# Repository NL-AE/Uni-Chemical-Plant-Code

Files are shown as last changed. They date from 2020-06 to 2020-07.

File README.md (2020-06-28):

# Uni-Chemical-Plant-Code
Code for two-way I2C communication between two Arduino nanos.
One drives the 2.4” TFT LCD display and the other controls all of the pumps.

The control Arduino also sends out serial data at 115200 baud rate in the format of:
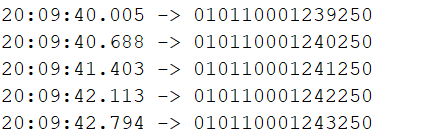
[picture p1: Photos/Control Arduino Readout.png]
Readout

Breakdown

Fresh interface in a simplified P&ID (Piping and instrumentation diagram)
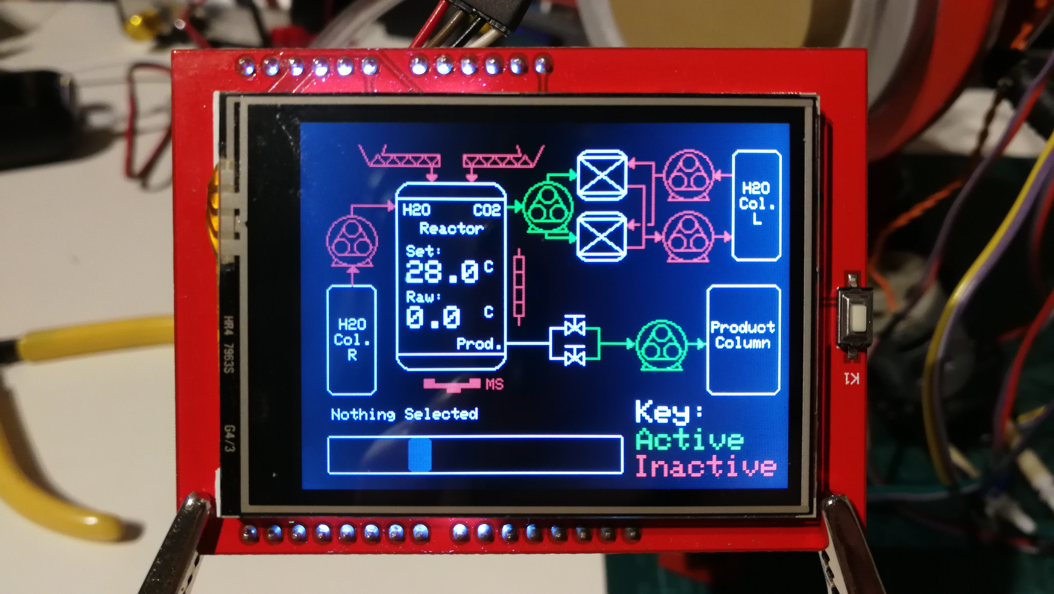
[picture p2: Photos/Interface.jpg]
Interface


Schematic
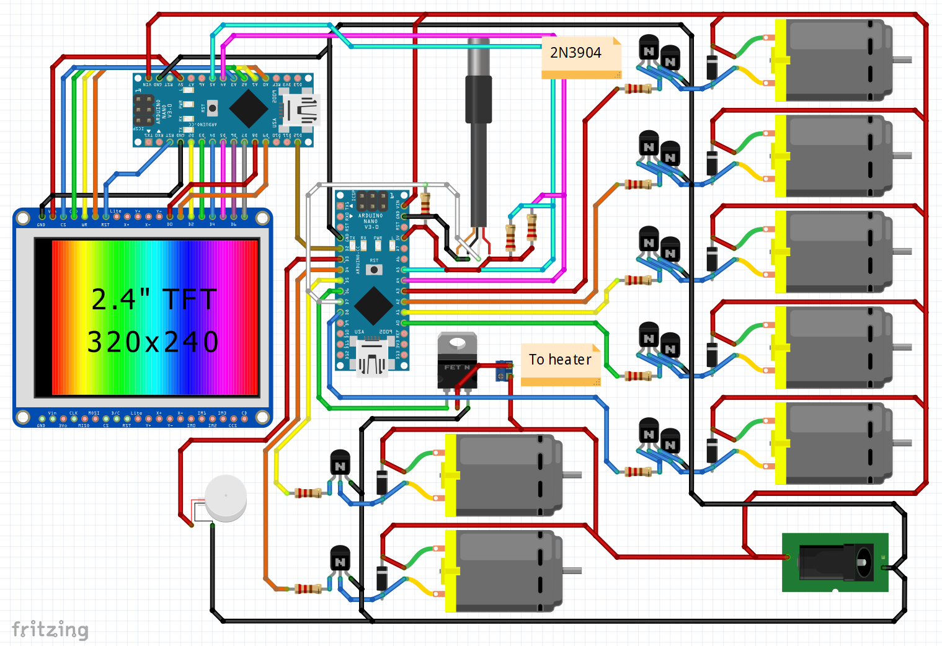
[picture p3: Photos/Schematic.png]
Schematic


Code Flowchart
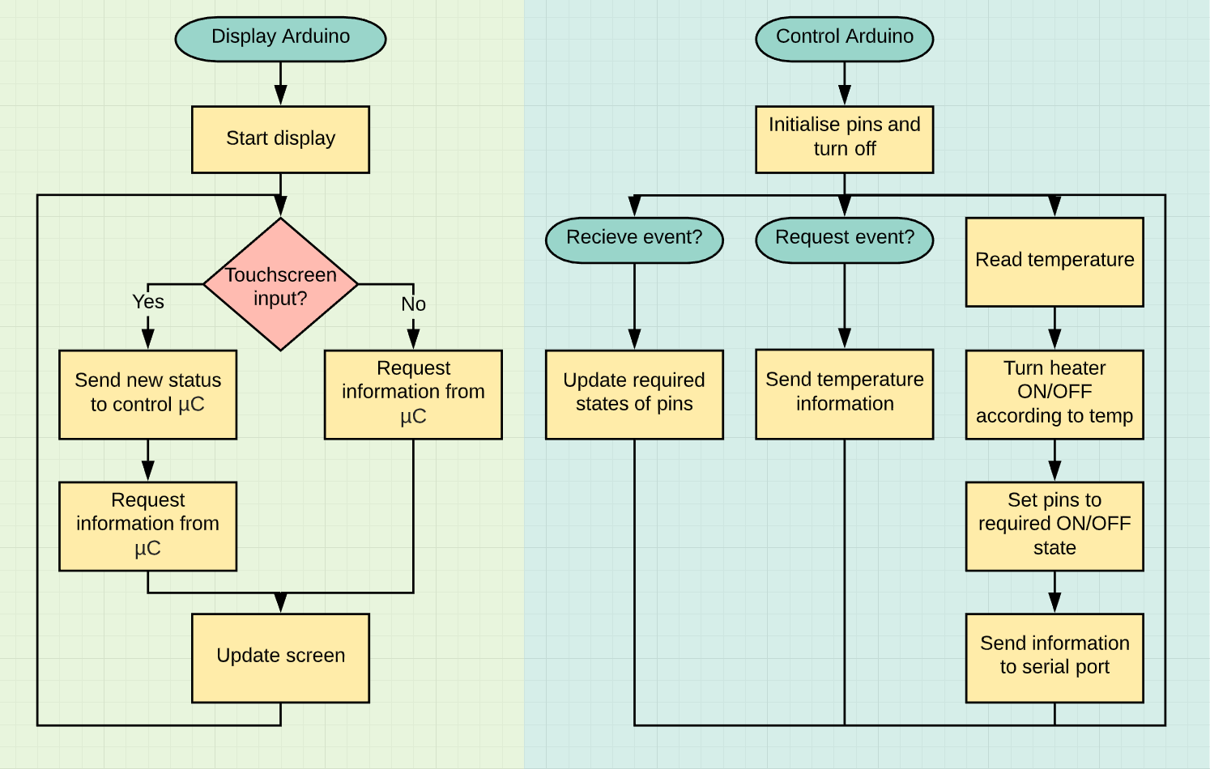
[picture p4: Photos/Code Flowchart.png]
Code_Flowchart


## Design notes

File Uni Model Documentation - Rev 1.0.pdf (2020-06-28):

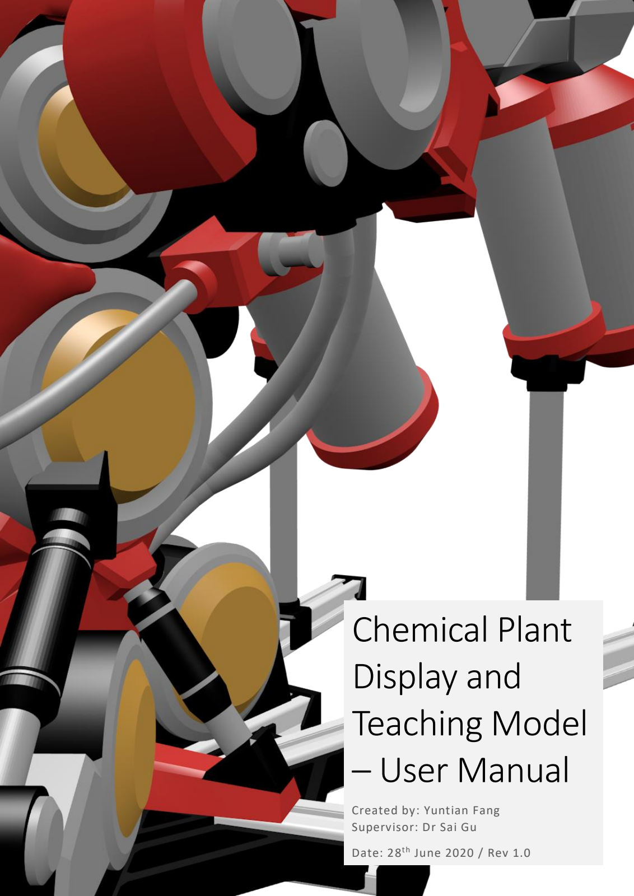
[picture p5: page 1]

# Chemical Plant Display and Teaching Model – User Manual

Created by: Yuntian Fang
Supervisor: Dr Sai Gu

Date: 28

th June 2020 / Rev 1.0

## Introduction

This fully 3D printed model of a basic chemical plant is intended to be used as a display and simple teaching model with all the functionality of a real chemical plant in an aesthetically appealing package.

Controlled by the touchscreen on the front and powered just by a generic 12V 3A mains plug, the model is entirely self-contained and is very simple to set up. It simply needs to be plugged in to power and the microprocessors will automatically begin.

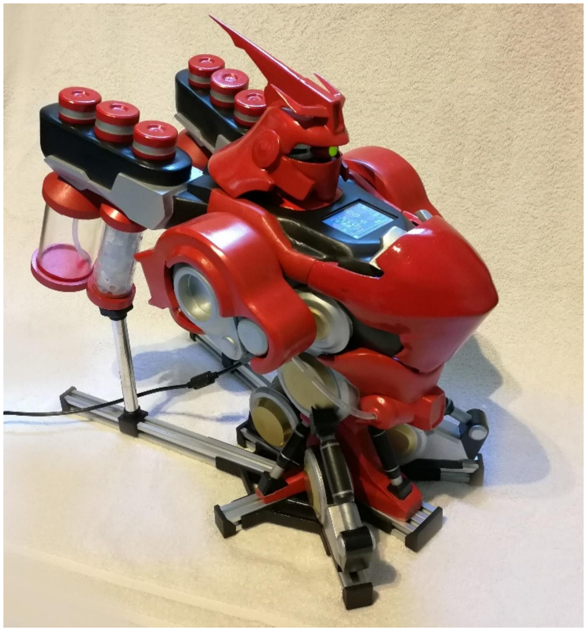
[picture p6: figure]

Figure 1: Fully assembled model powered on. Dimensions are (WxLxH): 25cm x 50cm x 43cm.

## Functionality

The model contains following parts:

- 2 x screw feeders into the main reactor for solid-based reactants.
- 1 x liquid reactant holder with delivery to reactor vessel (removable).
- 1 x CO2 extraction vessel using a water scrubbing system.
- 1 x CO2 scrubbing water storage vessel (removable).
- 1 x Reactant storage vessel (removable).
- 1 x Reactor vessel.
- Temperature controlled to the nearest 0.1oC.
- Magnetic stirrer.
- USB mini output to computer.
- 2.4” touchscreen with P&ID schematic interface.

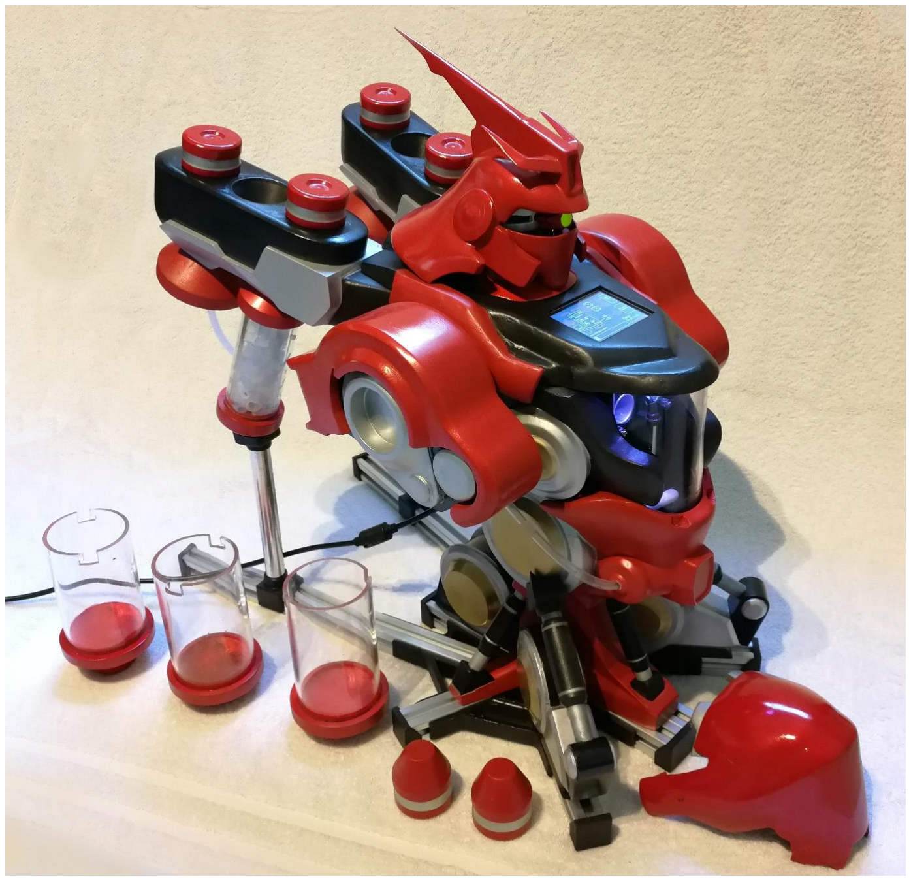
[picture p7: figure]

Figure 2: Model with parts removed exposing the reactor vessel and screw feeder input holes.

## Specific Areas of Interest

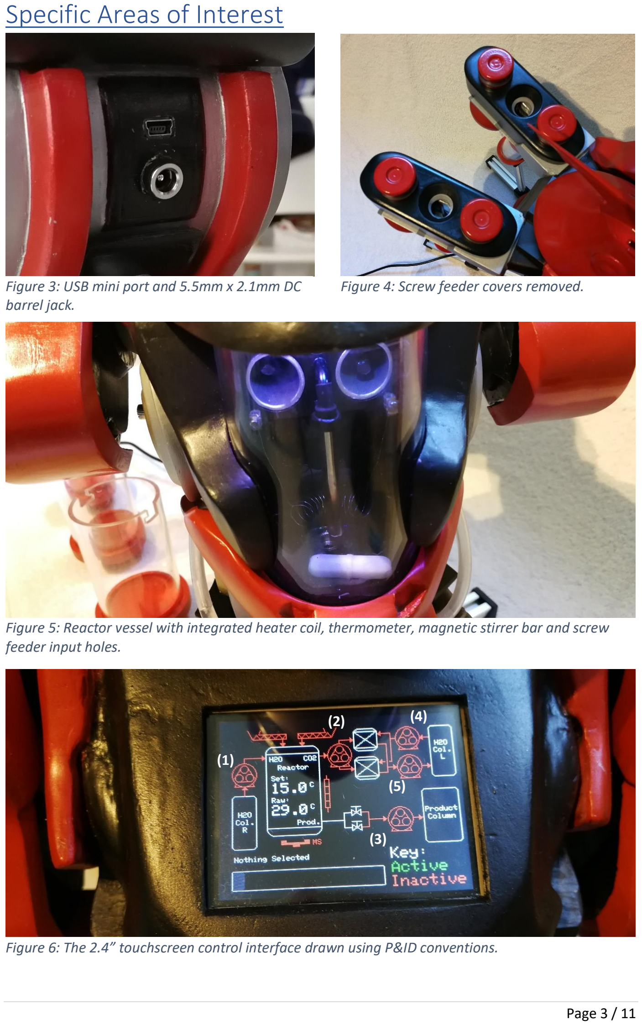
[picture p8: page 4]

Figure 3: USB mini port and 5.5mm x 2.1mm DC barrel jack.

Figure 4: Screw feeder covers removed.

Figure 5: Reactor vessel with integrated heater coil, thermometer, magnetic stirrer bar and screw feeder input holes.

Figure 6: The 2.4” touchscreen control interface drawn using P&ID conventions.

(1)

(2)

(3)

(4)

(5)

## Mode of Operation

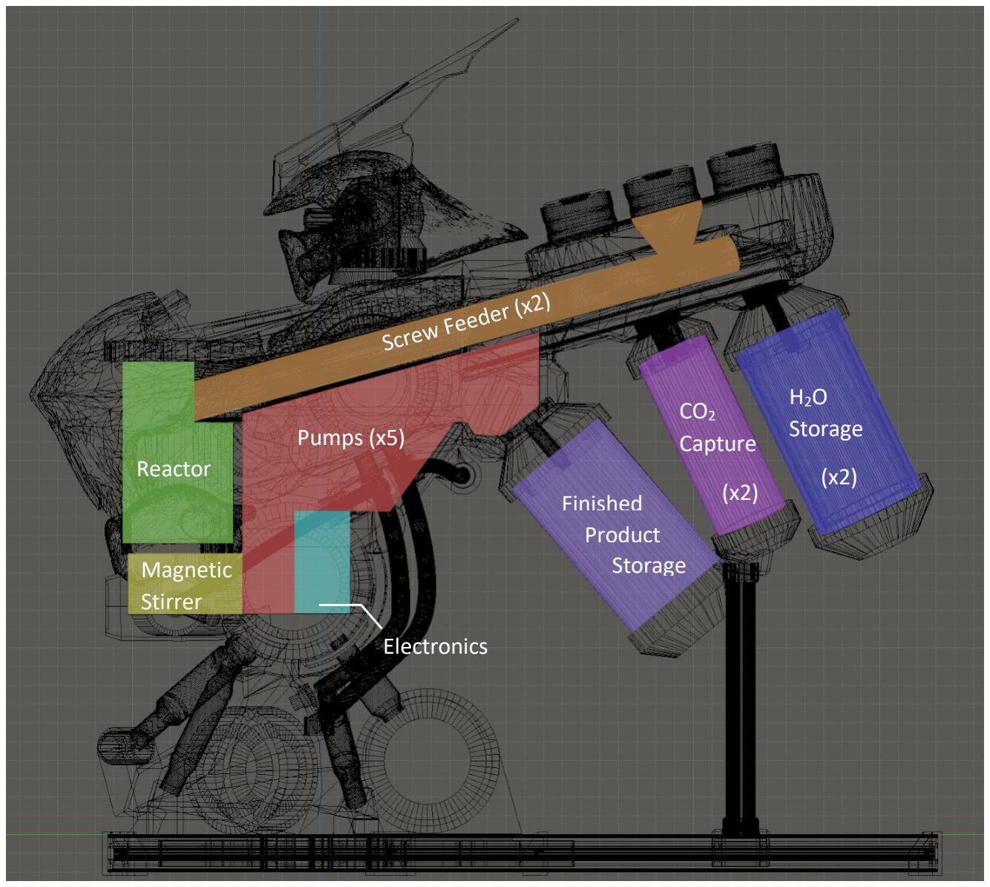
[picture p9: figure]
Reactor; Pumps (x5); Electronics; H2O Storage; CO2 Capture; Magnetic Stirrer; Finished Product Storage

Inside the model, there are five self-priming peristaltic pumps to move liquids around and two DC motors that control the screw feeders.

As per the P&ID diagram before,

- Pump 1 : Moves water from the H2O column on the right directly into the reactor.
- Pump 2 : Removes CO2 and transfers it to the CO2 capture column. Only the column on the left will function due to technical difficulties.
- Pump 3 : Transfers the liquid product from the reactor into the finished product storage column.
- Pump 4 : Supplies water to the CO2 scrubber from the H2O column on the left.
- Pump 5 : Returns water from CO2 scrubber back to left H2O column.

Figure 7: Highlighted and labelled areas of the model.

## Notes for Usage and Safety

1) Power and USB connection:
a. Power the model with a 12V supply (±1V) with at least 3A capability through the DC barrel jack.
b. Do NOT connect to computer without plugging into power BEFOREHAND.
c. ALWAYS remove USB connection BEFORE removing 12V power.
d. Failure to comply with notes 1b and 1c may cause the microcontroller to crash or other erratic behaviour not limited to permeant damage to the microcontroller and the PC it is connected to.
2) Operating pumps:
a. Do NOT allow the following pumps to operate without supervision.
i. Pump 1 – Moves water into the reactor.
ii. Pump 3 – Moves liquid from reactor to product storage. These pumps control liquid flow in and out of the reactor which can overflow.
This is due to the lack of feedback systems from the additional complexity of monitoring systems and hysteresis from the relatively large volume contained inside the connecting pipes.
b. Pumps 4 and 5 should be operational at the same time during continuous operation and should only differ during start-up (to add some water into the capture column) and during shut down (to remove all water from the column.)
c. Pump 2 can be operated in any situation.
3) Screw feeders:
a. Do NOT pour liquids into the mechanism. If cleaning is needed use compressed air or other non-liquid method.
b. Replace cover after use to prevent the screw from being jammed by any external objects that may enter.
4) Reactor and storage columns:
a. Do NOT allow reactor to overflow.
b. Empty them out after purging all water from system.
c. Do NOT set the heater temperature to higher than raw without there being water in the reactor.
5) Top cover
a. Can be removed and replaced to expose internals. Held on by friction. May require a gentle push to lock into place. Do not force.

## Design and Electronics

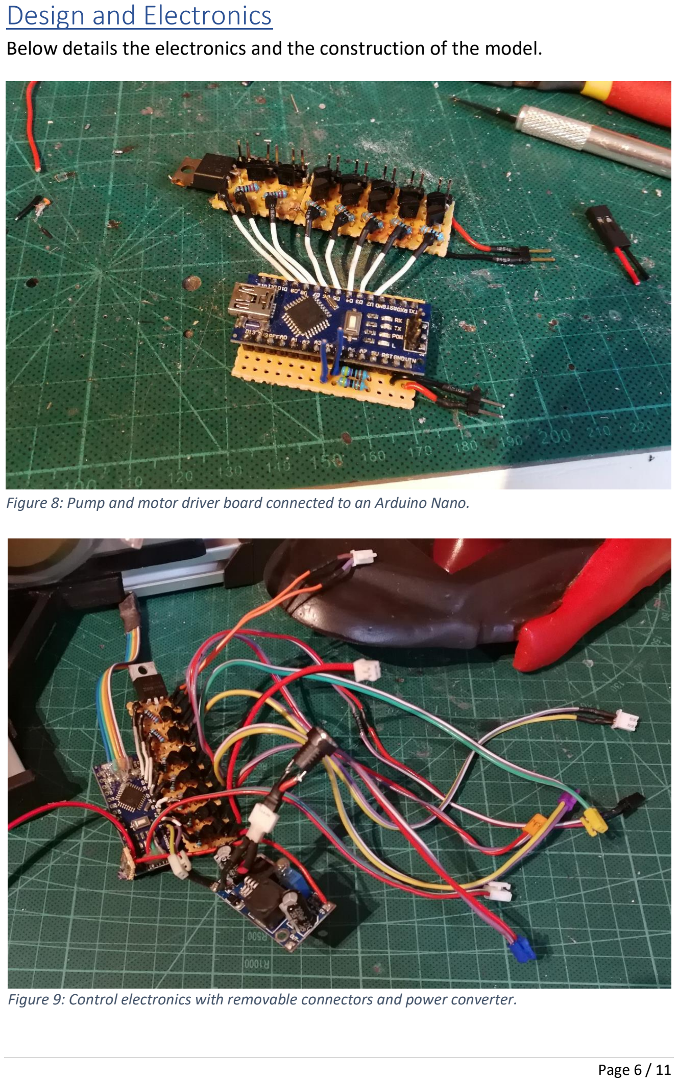
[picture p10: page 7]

Below details the electronics and the construction of the model.

Figure 8: Pump and motor driver board connected to an Arduino Nano.

Figure 9: Control electronics with removable connectors and power converter.

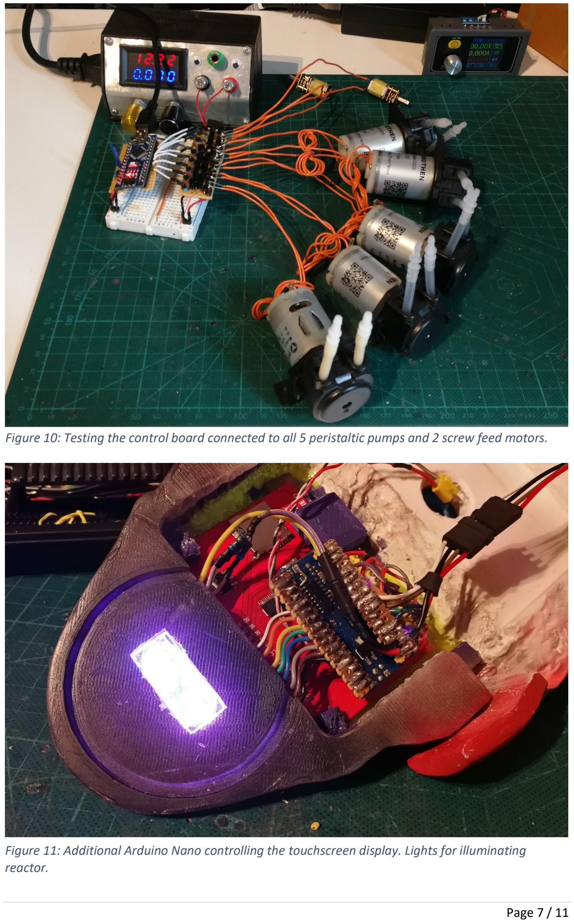
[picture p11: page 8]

Figure 10: Testing the control board connected to all 5 peristaltic pumps and 2 screw feed motors.

Figure 11: Additional Arduino Nano controlling the touchscreen display. Lights for illuminating reactor.

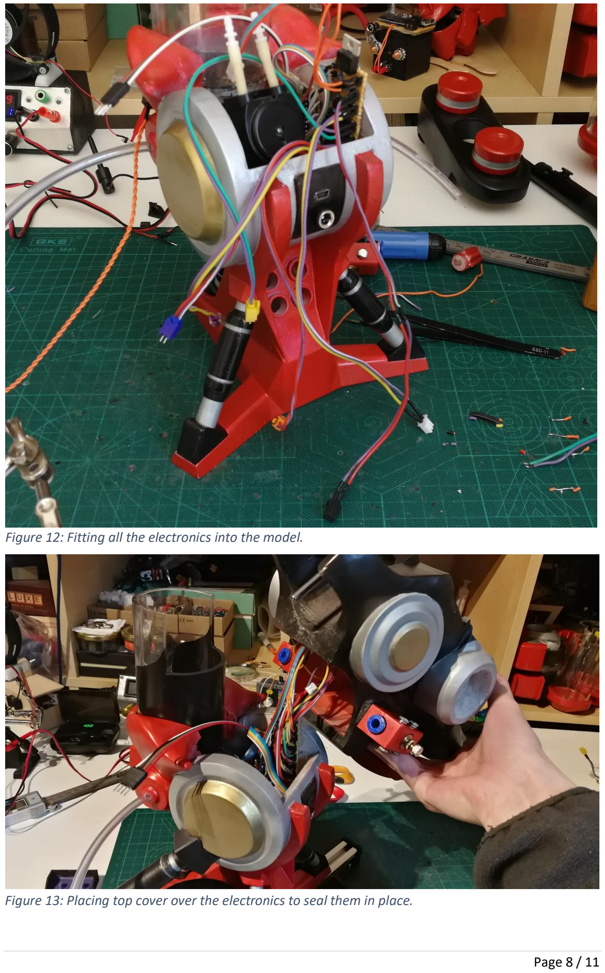
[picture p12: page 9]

Figure 12: Fitting all the electronics into the model.

Figure 13: Placing top cover over the electronics to seal them in place.

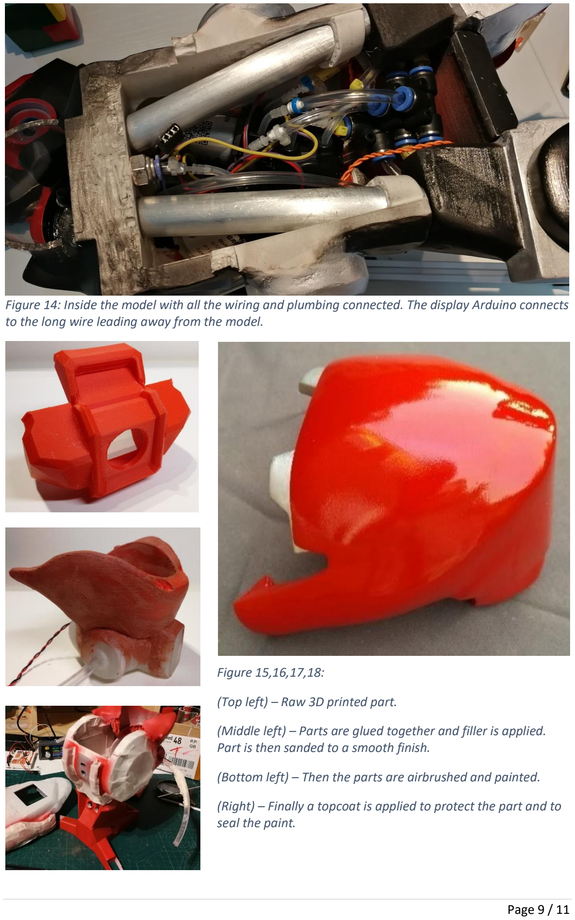
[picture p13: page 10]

Figure 14: Inside the model with all the wiring and plumbing connected. The display Arduino connects to the long wire leading away from the model.

Figure 15,16,17,18:

(Top left) – Raw 3D printed part.

(Middle left) – Parts are glued together and filler is applied. Part is then sanded to a smooth finish.

(Bottom left) – Then the parts are airbrushed and painted.

(Right) – Finally a topcoat is applied to protect the part and to seal the paint.

## References/Technical Information

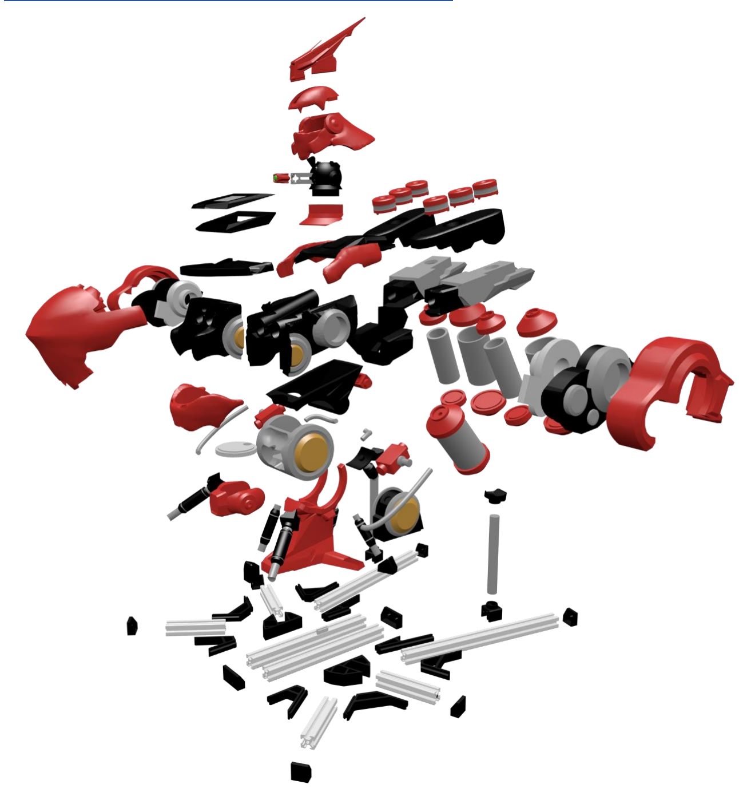
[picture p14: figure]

Following describes the more technical details of the model including the code and how the model operates.

The code can be freely downloaded at my GitHub:

https://github.com/NL-AE/Uni-Chemical-Plant-Code

The following information is also available on the README file in the GitHub and is copied here for convenience.

Figure 19: Exploded view of all the parts in the model.

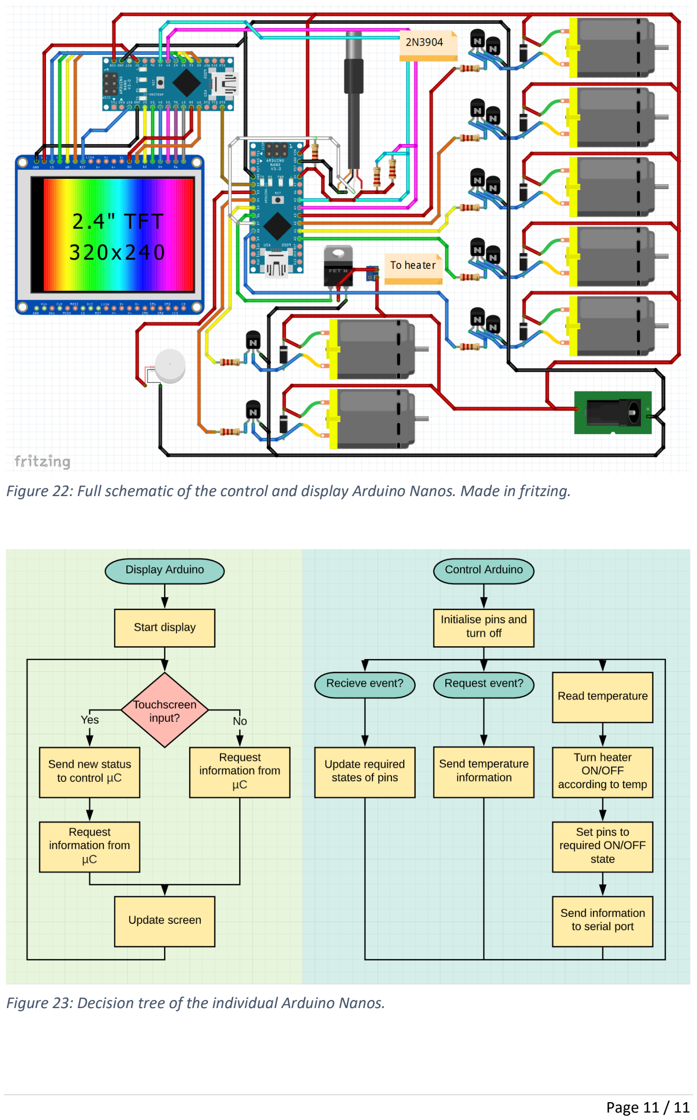
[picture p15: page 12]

Figure 22: Full schematic of the control and display Arduino Nanos. Made in fritzing.

Figure 23: Decision tree of the individual Arduino Nanos.

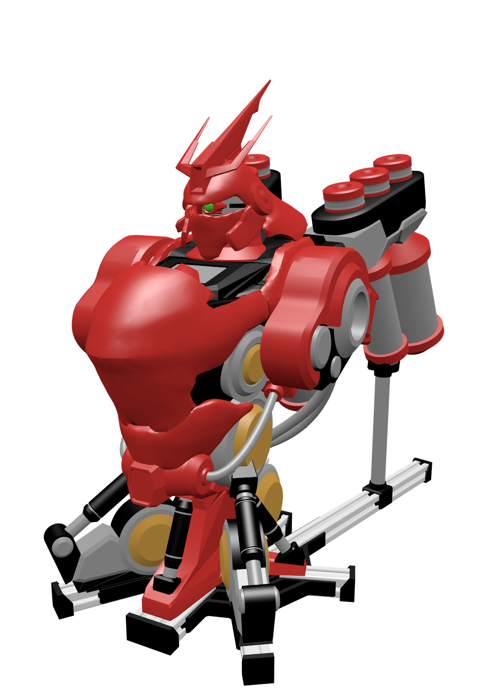
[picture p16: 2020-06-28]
Photos/3D Render.png

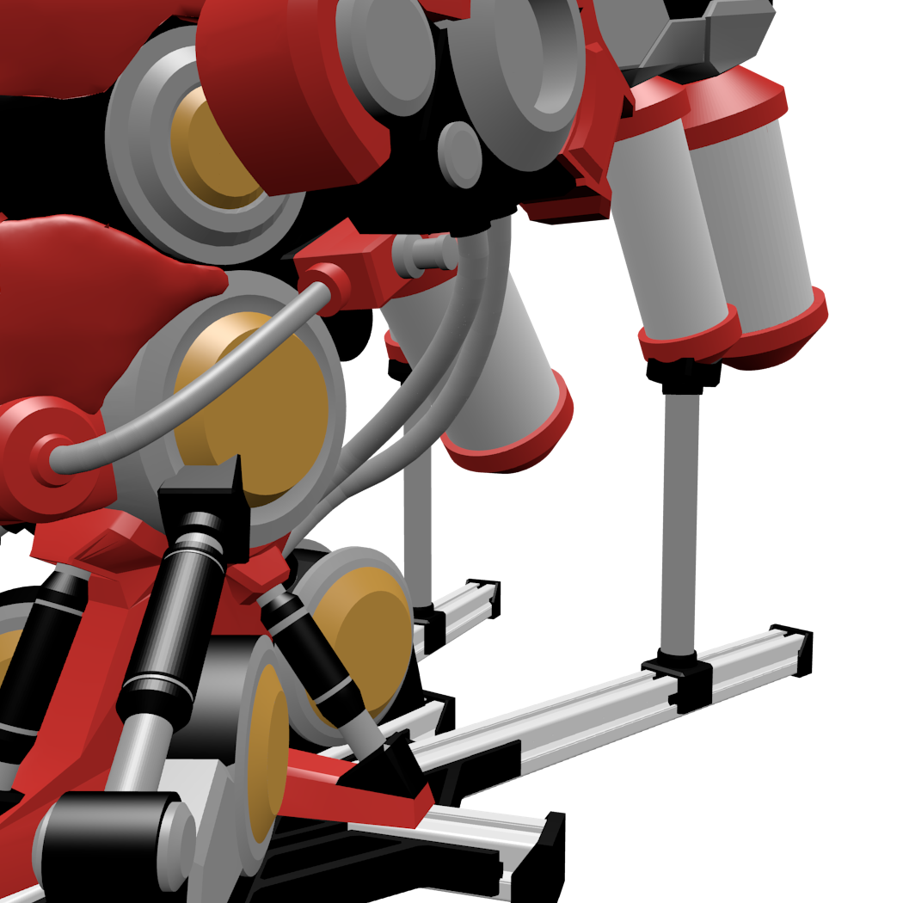
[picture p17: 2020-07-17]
Photos/Front - wide.png

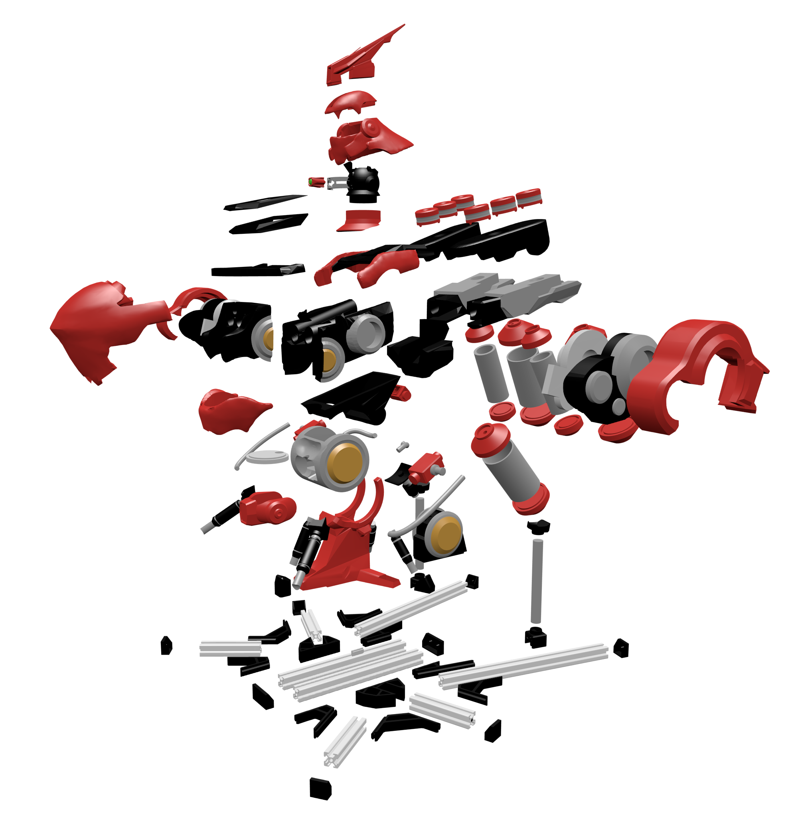
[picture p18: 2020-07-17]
Photos/Exploded.png

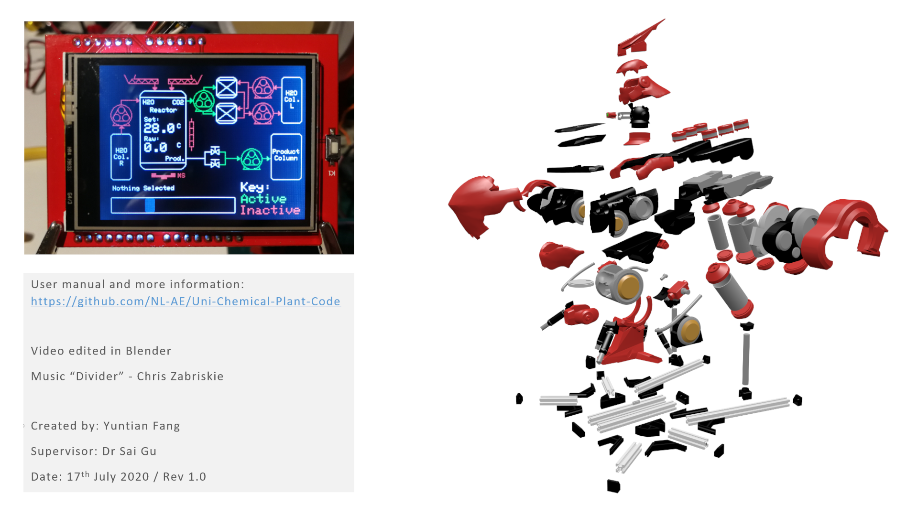
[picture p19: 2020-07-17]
Videos/Ending Card.png

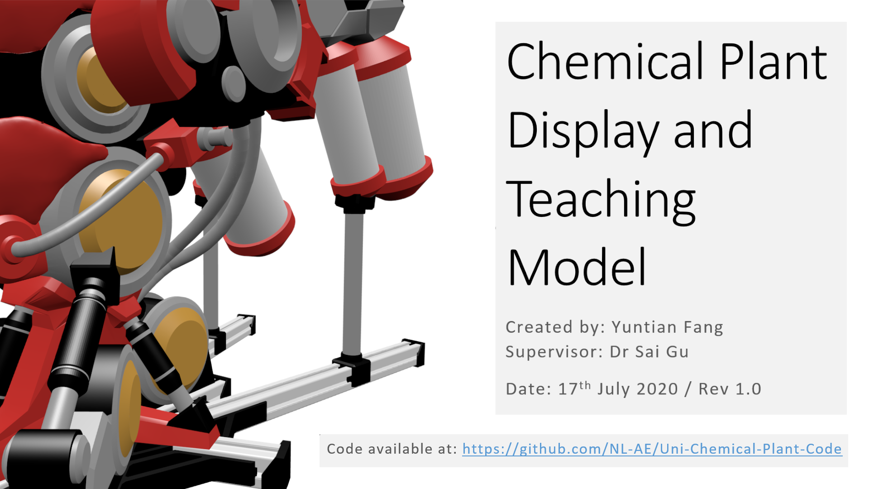
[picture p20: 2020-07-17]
Videos/Video Titlecard.png

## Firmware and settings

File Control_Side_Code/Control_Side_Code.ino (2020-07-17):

  // Libraries
    #include <Wire.h>                 // Wire for I2C
    #include <OneWire.h>              // For temp sensor
    #include <DallasTemperature.h>    // For temp sensor
    #define SOFTPWM_OUTPUT_DELAY      // Soft output for software PWM
    #include <PalatisSoftPWM.h>       // For Software PWM

  // Setup sensor
    #define ONE_WIRE_BUS 11               // Attach sensor to pin 11
    OneWire oneWire(ONE_WIRE_BUS);
    DallasTemperature sensors(&oneWire);

  // I2C Variables
    char responseChar[5];   // Response String for I2C to display master
    int SetTemp = 150;            // Store what the set temperature is
    
  // Define Pins    
    int pinArray[9] = {3,4,5,6,7,8,9,2,10};   // Pins for:  HtR, RtC, HtC, CtH, RtP, SFL, SFR, MS, EH
    int ActivePins[8] = {0,0,0,0,0,0,0,0};    // Status of: HtR, RtC, HtC, CtH, RtP, SFL, SFR, MS

    SOFTPWM_DEFINE_PIN2_CHANNEL(0);                 // Make pin 2 PWM channel 0
    SOFTPWM_DEFINE_OBJECT_WITH_PWM_LEVELS(1, 10);   // For 1 PWM channels, make them have 10 levels
    

  // Setup --------------------------------------------------------------
    void setup() {
      Serial.begin(115200);   // Serial begin
      sensors.begin();        // Setup temperature sensor

      PalatisSoftPWM.begin(60);  // begin with 60 Hz PWM frequency
  
      for(int i=0; i<9; i++){          // For loop (9 times)
        pinMode(pinArray[i],OUTPUT);      // Initialise pin as output
        digitalWrite(pinArray[i],LOW);    // Switch pin off
      }

      // I2C
        Wire.begin(9);                  // Begin as I2C slave with address 9
        Wire.onRequest(requestEvent);   // Function when data requested
        Wire.onReceive(receiveEvent);   // Function when data recieved
    }

  // Loop  --------------------------------------------------------------
    void loop() {
      sensors.requestTemperatures();                // Request temps
      int RawTemp = 10*sensors.getTempCByIndex(0);  // Read raw temperature and times it by 10 to make it int
      int HeaterStatus;

      if(RawTemp<SetTemp){
        digitalWrite(pinArray[8],1);                // If raw temp. < set temp. turn heater on
        HeaterStatus = 1;
      }else{
        digitalWrite(pinArray[8],0);                // If raw temp. > set temp. turn heater off
        HeaterStatus = 0;
      }

      for(int i=0; i<7; i++){
        digitalWrite(pinArray[i],ActivePins[i]);    // Write to all pins correct states
      }

      if(ActivePins[7]==1){
        PalatisSoftPWM.set(0, 9);
      }else{
        PalatisSoftPWM.set(0, 0);
      }
      
      String response = String(RawTemp) + String(HeaterStatus);   // Create response string (sending in format of: 4501 which means read temperature is 45.0C and heater is on)
      response.toCharArray(responseChar, 5);                      // Make into char array

      // Printing to Serial
        for(int i=0; i<8; i++){         // For loop 8 times
          Serial.print(ActivePins[i]);    // Print status of all pins
        }
        Serial.print(HeaterStatus);       // Print heater status
        Serial.print(RawTemp);            // Print raw temperature
        Serial.println(SetTemp);          // Print set temperature        
    }
    
  // Recieve Event ------------------------------------------------------
    void receiveEvent(int howMany) {
      int i=0;                          // make i variable
      
      while (1 < Wire.available()) {  // loop through until we get to the last bit
        ActivePins[i] = Wire.read();  // recieve byte and put in array
        i++;                          // increment i variable (so we can assign the bit to the chronological place in the array)
      }
      
      SetTemp = Wire.read()*10.;    // receive final byte as an integer
    }

  // Request Event ------------------------------------------------------
    void requestEvent() {
      Wire.write(responseChar);     // Send previously made char array
    }





  // --------------------------------------------------------------------

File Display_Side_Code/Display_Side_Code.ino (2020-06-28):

 
  // Libraries
    #include <Adafruit_GFX.h>     // Adafruit GFX library
    #include <TouchScreen.h>      // Touchscreen
    #include <Adafruit_TFTLCD.h>  // Adafruit TFT
    #include <Wire.h> 
    
  // Display Declecation
    Adafruit_TFTLCD tft(A3, A2, A1, A0, A4);            // Pins for TFT 
    TouchScreen ts = TouchScreen(8, A3, A2, 9, 300);    // Pins for Touchscreen

    #define TimeToDeselect 3000     // Miliseconds for when it deselects
    long TimeWhenTouched;
    int SetTemp = 15.0;

  //Colours
    #define W  0xF79E  // White
    #define B  0x001E  // Blue
    #define R  0xF000  // Red
    #define G  0x26A0  // Green
    #define GR 0x94B2  // Grey
    #define N  0x0000  // Black

  // Misc Variables
    long ColourState[8]  = {0,0,0,0,0,0,0,0};   // Stores the colour state of all clickable things

  // Setup --------------------------------------------------------------
    void setup() {
      Serial.begin(115200);   // Start serial       
      Wire.begin();           // Begin as master
      SetupDisplay();         // Setup display and also draws everything for first time
    }

  // Loop ---------------------------------------------------------------
    void loop() {

      // Get touchpoint
        TSPoint p = ts.getPoint();    
        pinMode(A2, OUTPUT);
        pinMode(A3, OUTPUT);

      // If user touches screen
        if(p.z > 10){
          int XPos = map(p.y, 80,890,320,  0);  // Map x
          int YPos = map(p.x,110,910,  0,240);  // Map y
          
          tft.setTextColor(W,N);  tft.setTextSize(1);  tft.setCursor(20,187);  
  
          // Find where the user selected - im only going to comment one of these since the only thing that changes between them is the co-ordinates and the array number
            if( XPos> 13 && XPos< 55 && YPos> 57 && YPos< 99){  // H2O -> Reactor pump
              
              tft.print(F("H2O -> Reactor Pump ")); // Print what thing you selected
              TimeWhenTouched = millis();
              
                ColourState[0]++;           // Increment touch counter                
                if(ColourState[0]%2 == 1){  // Check if divisible by two
                  DrawHtR(G);                 // No, change it to green
                }else{
                  DrawHtR(R);                 // Yes, change it back to red
                }              
            }
            if( XPos>141 && XPos<183 && YPos> 34 && YPos< 76){  // Reactor -> CO2 pump
              tft.print(F("Reactor -> CO2 Pump "));
              TimeWhenTouched = millis();
                ColourState[1]++;
                if(ColourState[1]%2 == 1){
                  DrawRtC(G);
                }else{
                  DrawRtC(R);
                }              
            }
            if( XPos>233 && XPos<275 && YPos> 14 && YPos< 56){  // H2O -> CO2 pump
              tft.print(F("H2O -> CO2 Pump     "));
              TimeWhenTouched = millis();
                ColourState[2]++;
                if(ColourState[2]%2 == 1){
                  DrawHtC(G);
                }else{
                  DrawHtC(R);
                }
            }
            if( XPos>233 && XPos<275 && YPos> 54 && YPos< 96){  // CO2 -> H2O pump
              tft.print(F("CO2 -> H2O Pump     "));
              TimeWhenTouched = millis();
                ColourState[3]++;
                if(ColourState[3]%2 == 1){
                  DrawCtH(G);
                }else{
                  DrawCtH(R);
                }
            }
            if( XPos>216 && XPos<258 && YPos>125 && YPos<167){  // Reactor -> Products
              tft.print(F("React. -> Prod. Pump"));
              TimeWhenTouched = millis();
                ColourState[4]++;
                if(ColourState[4]%2 == 1){
                  DrawRtP(G);
                }else{
                  DrawRtP(R);
                }
            }
            if( XPos> 30 && XPos< 98 && YPos>  7 && YPos< 36){  // L Screw Feed
              tft.print(F("L Screw Feed        "));
              TimeWhenTouched = millis();
                ColourState[5]++;
                if(ColourState[5]%2 == 1){
                  DrawSFL(G);
                }else{
                  DrawSFL(R);
                }
            }
            if( XPos> 99 && XPos<166 && YPos>  7 && YPos< 36){  // R Screw Feed
              tft.print(F("R Screw Feed        "));
              TimeWhenTouched = millis();
                ColourState[6]++;
                if(ColourState[6]%2 == 1){
                  DrawSFR(G);
                }else{
                  DrawSFR(R);
                }
            }
            if( XPos> 69 && XPos<139 && YPos>163 && YPos<192){  // Mag Stirrer
              tft.print(F("Magnetic Stirrer    "));
              TimeWhenTouched = millis();
                ColourState[7]++;
                if(ColourState[7]%2 == 1){
                  DrawMS(G);
                }else{
                  DrawMS(R);
                }
            }

            // This one draws a draggable slider
            if( XPos> 17 && XPos<222 && YPos>205 && YPos<230){  // Set temperature
              tft.print(F("Changing Set Temp   "));
              TimeWhenTouched = millis();

              // Draw Slider
                tft.fillRoundRect( 18,206,192, 23, 3, N);                 // Black Background
                int sliderX = constrain(map(p.y, 80,890,320,0),19,195);   // Constrain and map touch X co-ord
                tft.fillRoundRect(sliderX,206, 15, 23, 3, GR);            // Move Slider

              // Set Temperature
                SetTemp = map(sliderX,19,195,15,60);          // Map slider position to set temp between 15C and 60C
                tft.setTextColor(W,N);  tft.setTextSize(2);
                tft.setCursor(69,90); tft.print(SetTemp);     // Print the set temperature
            }

            // Now Send I2C Data
              Wire.beginTransmission(9);        // Send to slave with address 9
              for(int i=0; i<8; i++){
                Wire.write(ColourState[i]%2);   // Send the colour of all the selectables by accessing the precious array
              }
              Wire.write(SetTemp);              // Send the set temperature
              Wire.endTransmission();           // End transmission
        }

      // Deselect
        if((millis()-TimeWhenTouched) > TimeToDeselect){    // Deselect after number of seconds
          tft.setTextColor(W,N);  tft.setTextSize(1);
          tft.setCursor(20,187);  tft.print(F("Nothing Selected    "));
          }
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
